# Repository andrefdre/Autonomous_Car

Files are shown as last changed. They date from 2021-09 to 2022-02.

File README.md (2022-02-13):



<!-- PROJECT SHIELDS -->
<!--
*** I'm using markdown "reference style" links for readability.
*** Reference links are enclosed in brackets [ ] instead of parentheses ( ).
*** See the bottom of this document for the declaration of the reference variables
*** for contributors-url, forks-url, etc. This is an optional, concise syntax you may use.
*** https://www.markdownguide.org/basic-syntax/#reference-style-links
-->
[][contributors-url]
[][forks-url]
[][stars-url]
[][issues-url]
[][license-url]
[][linkedin-url]

<!-- PROJECT LOGO -->
<br />
<div align="center">
  <a href="https://github.com/andrefdre/Autonomous_Car">
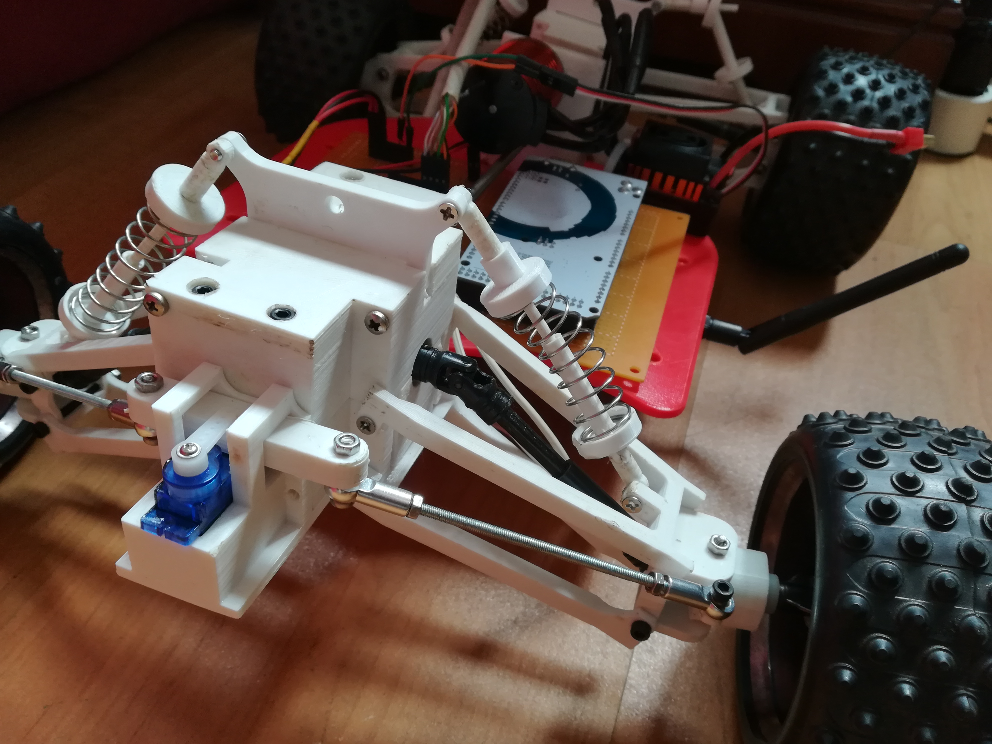
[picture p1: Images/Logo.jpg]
    
  </a>

  <h3 align="center">Autonomous Car</h3>

  <p align="center">
    It's an atounomous car that uses GPS.
    <br />
    <br />
    <a href="https://github.com/andrefdre/Carro/issues">Issues</a>
    ·
    <a href="https://github.com/andrefdre/Carro/projects/1">Project</a>
    ·
    <a href="https://github.com/andrefdre/Carro/wiki">Wiki</a>
  </p>
</div>

<!-- TABLE OF CONTENTS -->
<details>
  <summary>Table of Contents</summary>
  <ol>
    <li><a href="#Introduction">Introducion</a></li>
    <li><a href="#Libraries">Libraries</a> </li> 
    <li><a href="#License">License</a></li>
    <li><a href="#Contact">Contact</a></li>
  </ol>
</details>

<!-- Introduction -->
## Introduction

<p>This projected started in the beggining of my university and I setup myself to build an autonumous car that could drive alone. </p>
<p>The main objective was to make the car and add GPS navigation so it could have coordinates previously set up and then run that course. </p>
<p>So it all started with the mechanical part of the project with the palns to be 4 wheel drive and have a better suspension than the previous version. The components were mostly 3D printed and only the shafts and some other parts where bought. </p>
<p>After that, started the developemnt of the eletrical componnets alongside the programming of the code. This part was the most difficult since I had lots of problems with the communication beetwen the car and the controller.  </p>
<p>The previous version used bluetoth chips but since the range was very limited i eventualy changed to RF24 chips wich use radio waves that has more range.  </p>

<p> Previous version: </p> 
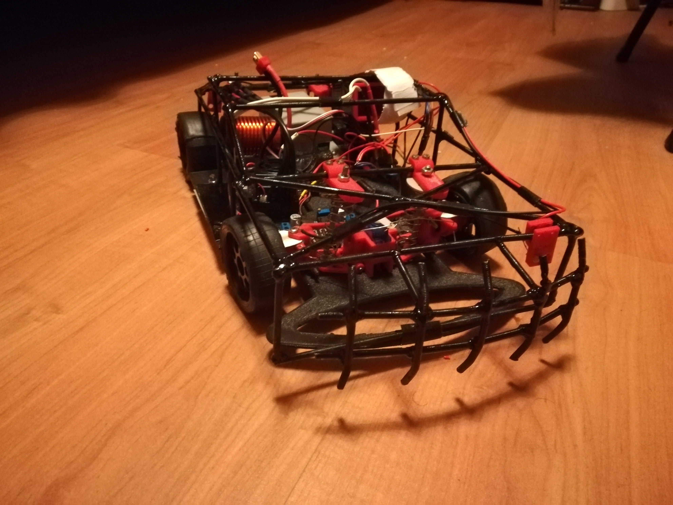
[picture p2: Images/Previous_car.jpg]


For more see the [open issues](https://github.com/andrefdre/Carro/issues) for a full list of proposed features (and known issues).

<p align="right">(<a href="#top">back to top</a>)</p>

<!-- Required_Libraries -->
## Libraries 

The arduino code requires some dependencies:
<ol>
    <li><a href="https://github.com/embeddedartistry/arduino-printf">LibPrintf</a></li>
    <li><a href="https://forum.hobbycomponents.com/viewtopic.php?t=2034">HCPCA9685</a> </li> 
    <li><a href="https://www.arduino.cc/en/reference/SPI">SPI</a></li>
    <li><a href="https://github.com/nRF24/RF24">RF24</a></li>
    <li><a href="https://www.arduino.cc/reference/en/libraries/libprintf/">LibPrintf</a></li>
  </ol>

<p align="right">(<a href="#top">back to top</a>)</p>

<!-- LICENSE -->
## License

Distributed under the GNU GENERAL PUBLIC LICENSE. See `LICENSE.txt` for more information.

<p align="right">(<a href="#top">back to top</a>)</p>

<!-- CONTACT -->
## Contact

André Cardoso - andref@ua.pt

Project Link: [https://github.com/andrefdre/Carro](https://github.com/andrefdre/Carro)

<p align="right">(<a href="#top">back to top</a>)</p>

<!-- MARKDOWN LINKS & IMAGES -->
<!-- https://www.markdownguide.org/basic-syntax/#reference-style-links -->
[contributors-shield]: https://img.shields.io/github/contributors/andrefdre/Carro.svg?style=for-the-badge
[contributors-url]: https://github.com/andrefdre/Carro/graphs/contributors
[forks-shield]: https://img.shields.io/github/forks/andrefdre/Carro.svg?style=for-the-badge
[forks-url]: https://github.com/andrefdre/Carro/network/members
[stars-shield]: https://img.shields.io/github/stars/andrefdre/Carro.svg?style=for-the-badge
[stars-url]: https://github.com/andrefdre/Carro/stargazers
[issues-shield]: https://img.shields.io/github/issues/andrefdre/Carro.svg?style=for-the-badge
[issues-url]: https://github.com/andrefdre/Carro/issues
[license-shield]: https://img.shields.io/github/license/andrefdre/Carro.svg?style=for-the-badge
[license-url]: https://github.com/andrefdre/Carro/blob/main/LICENSE
[linkedin-shield]: https://img.shields.io/badge/-LinkedIn-black.svg?style=for-the-badge&logo=linkedin&colorB=555
[linkedin-url]: https://www.linkedin.com/in/andr%C3%A9-cardoso-8bb264223/
[product-screenshot]: Images/Logo.jpg

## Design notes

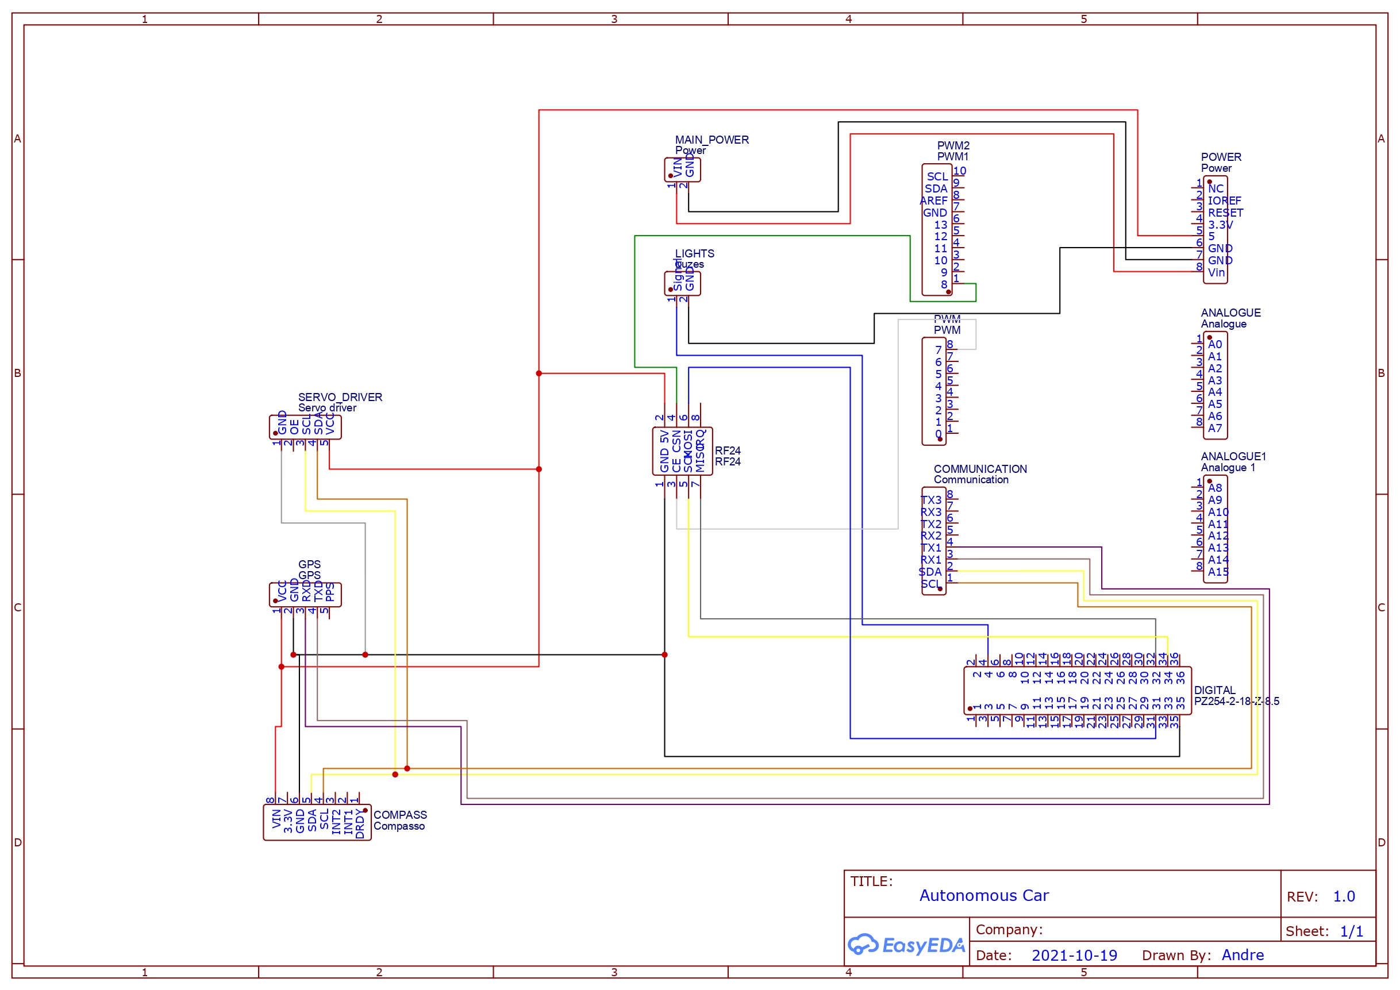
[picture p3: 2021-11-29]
Images/Schematic_Car.jpg

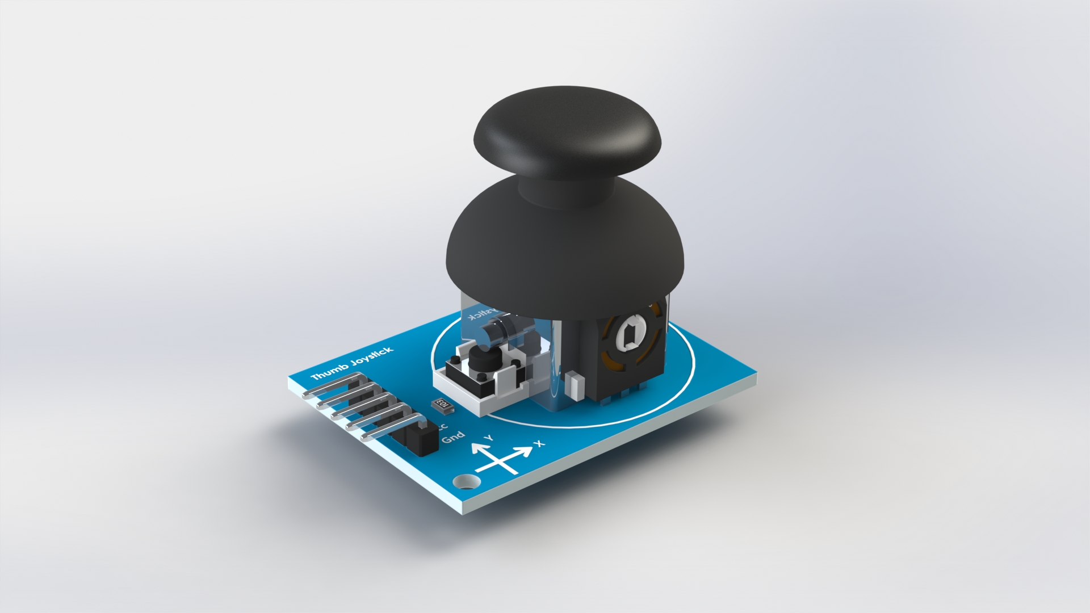
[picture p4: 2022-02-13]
Mechanical_project.psd/Controller/Imported/Joystick/PS2 Joystick Module 3D View.JPG

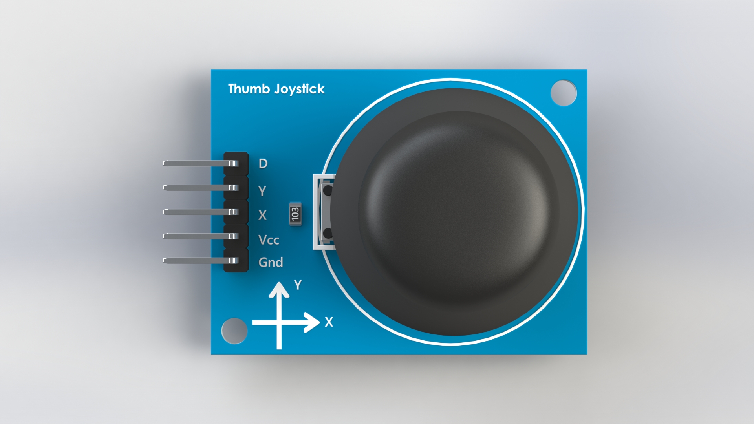
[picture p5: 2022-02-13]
Mechanical_project.psd/Controller/Imported/Joystick/PS2 Joystick Module Top View.JPG

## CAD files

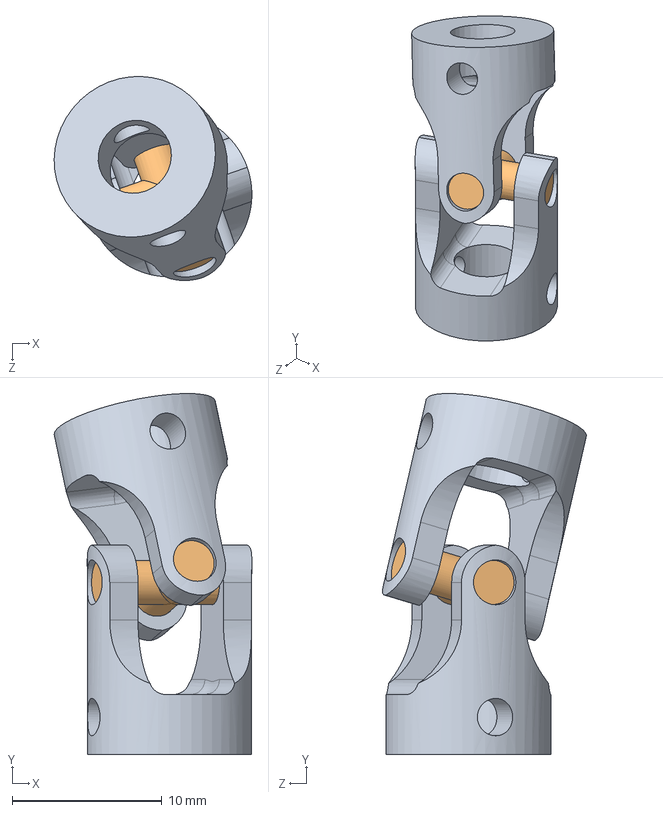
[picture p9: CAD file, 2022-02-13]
Mechanical_project.psd/Car/assemblie/U-joint.SLDASM
13.2 x 24.1 x 13.6 mm
u-joint x 2
u-joint middle

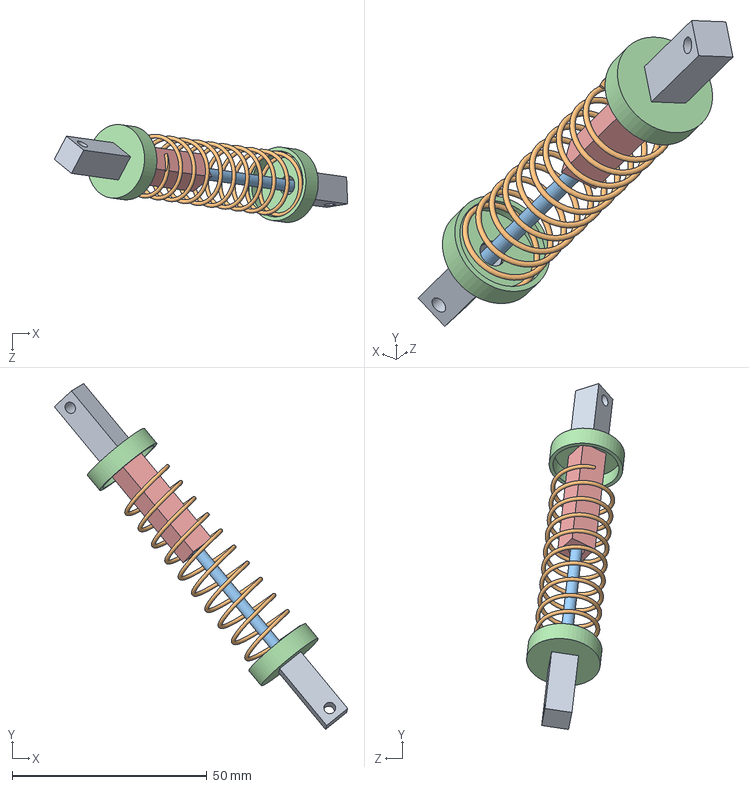
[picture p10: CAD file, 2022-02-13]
Mechanical_project.psd/Car/suspension/suspension rear left.SLDASM
75.3 x 88.8 x 25.2 mm
ball joint x 2
Spring
suspension shaft
washer x 2
suspension shaft 1

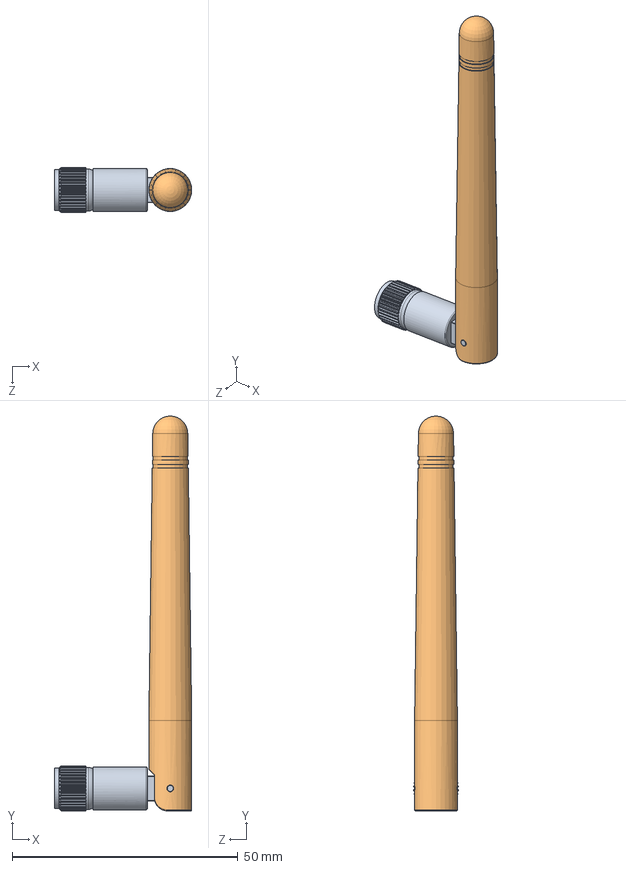
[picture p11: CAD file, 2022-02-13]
Mechanical_project.psd/downloaded/nrf24/NRF24L01L + Antenna 2.4 GHz/Antenna assy.SLDASM
30.5 x 87.5 x 9.98 mm
Antenna base
Antenna top

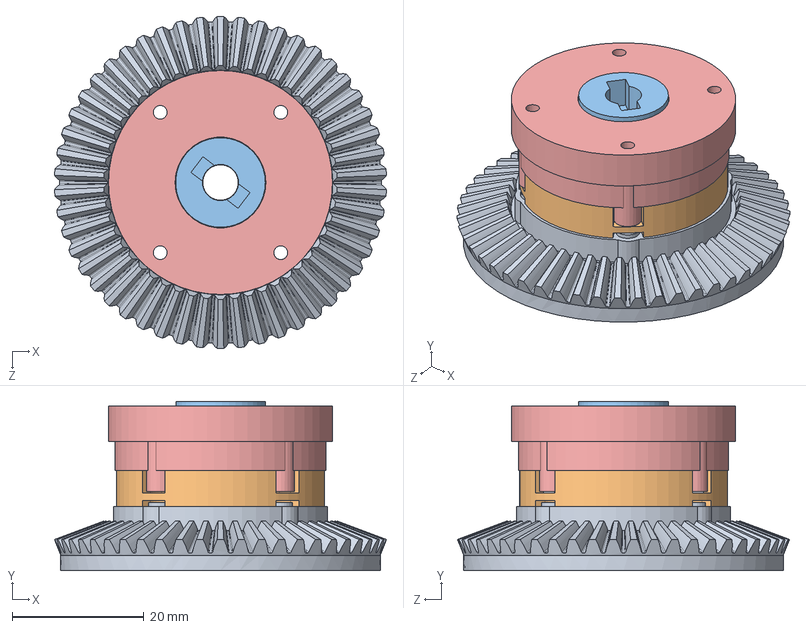
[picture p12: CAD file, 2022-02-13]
Mechanical_project.psd/Car/assemblie/Diferencial rodas.SLDASM
50.4 x 25.7 x 50.4 mm
anel versao 3
planeta x 2
sol x 2

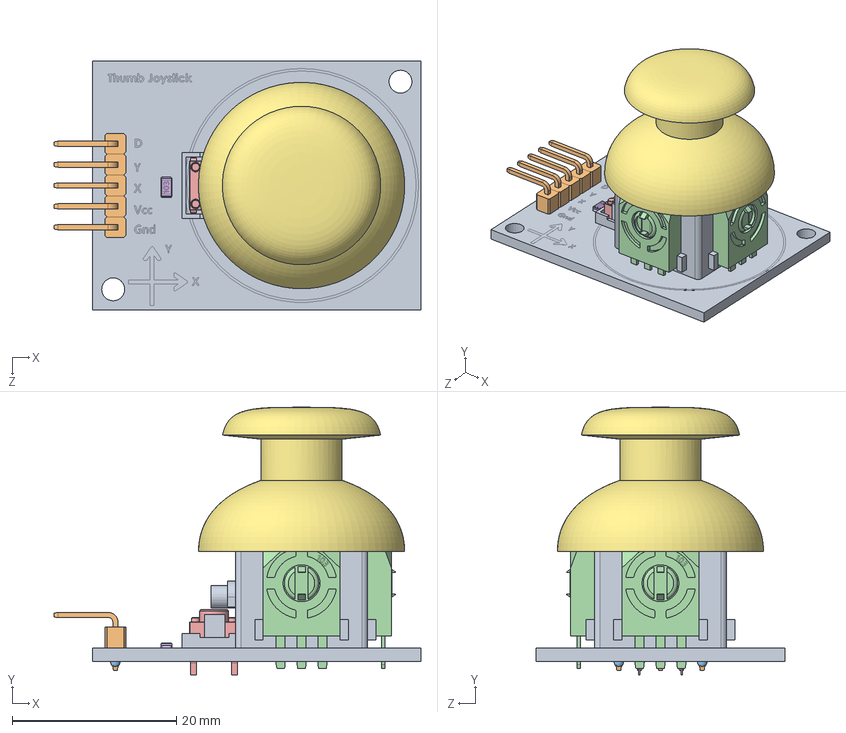
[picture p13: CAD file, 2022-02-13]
Mechanical_project.psd/Controller/Imported/Joystick/PS2 Joystick Module.SLDASM
44.7 x 32.6 x 30.3 mm
ps2board
90headerMale x 5
solder x 5
verticalTrimmer103 x 2
pushButton1_5mm
smdResistor103
Thumbstick

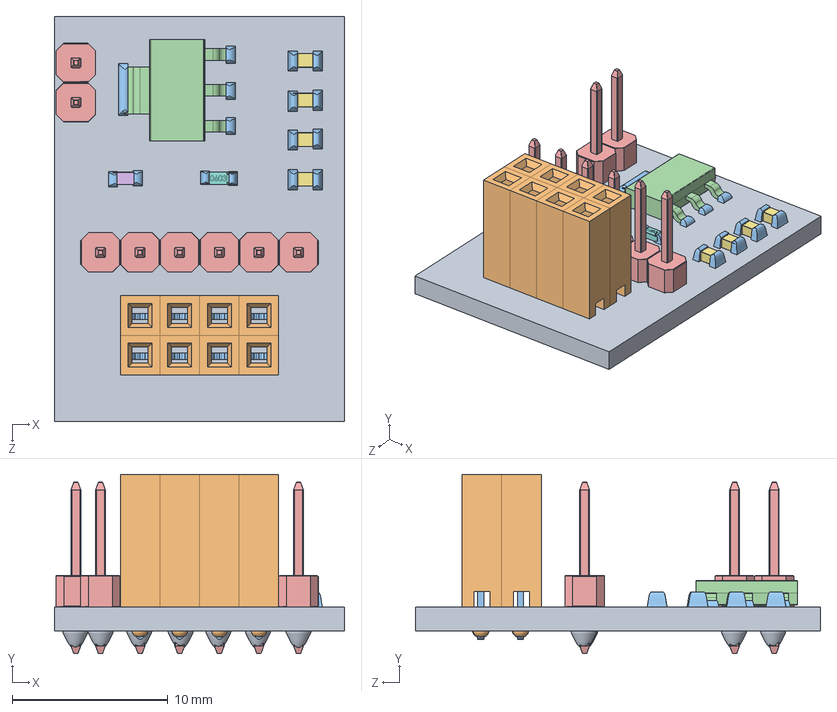
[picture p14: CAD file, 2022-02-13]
Mechanical_project.psd/downloaded/nrf24/NRFL24L01_Power_Board_asm.SLDASM
18.6 x 11.5 x 26.0 mm
nRF24L01_power_board_PCB
header x 8
pin x 8
SOT-223
Strait_Headers x 2
User Library-LED 0603
User Library-CAPC1608X09 x 4
User Library-RES_1609-0603
Solder x 9
Solder2 x 8
Solder3 x 16

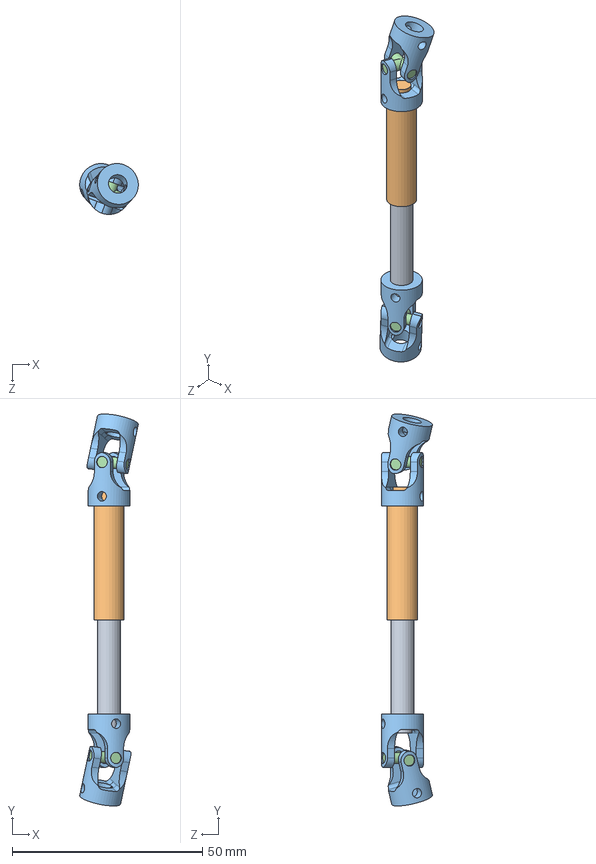
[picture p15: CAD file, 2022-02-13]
Mechanical_project.psd/Car/assemblie/Ujoin axle.SLDASM
15.4 x 102.9 x 13.4 mm
eixo ujoint inner
eixo ujoint outside
u-joint x 4
u-joint middle x 2

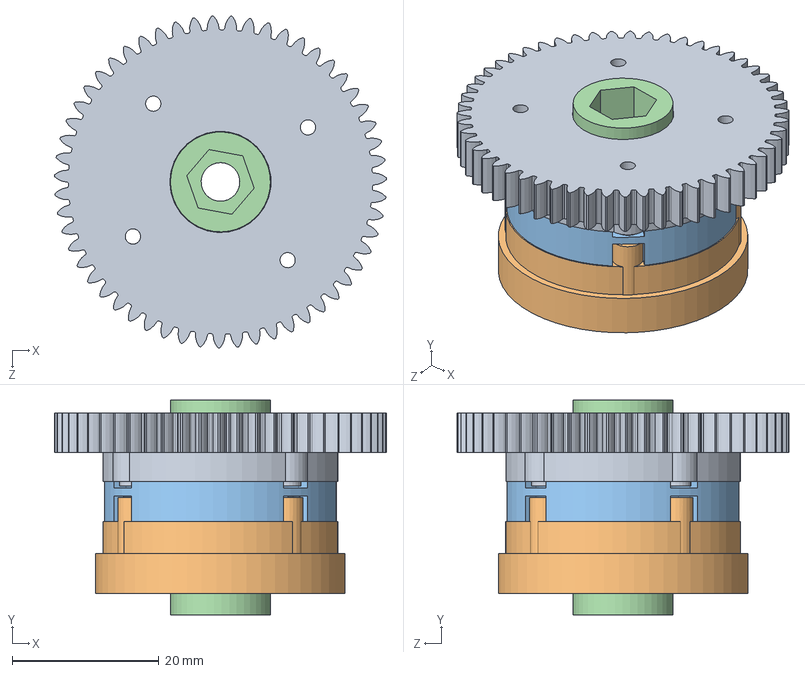
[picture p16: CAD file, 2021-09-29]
Mechanical_project.psd/Car/assemblie/planetery.SLDASM
45.2 x 29.3 x 45.2 mm
anel
anel 2
middle part of the planetery
planeta x 2
sol x 2

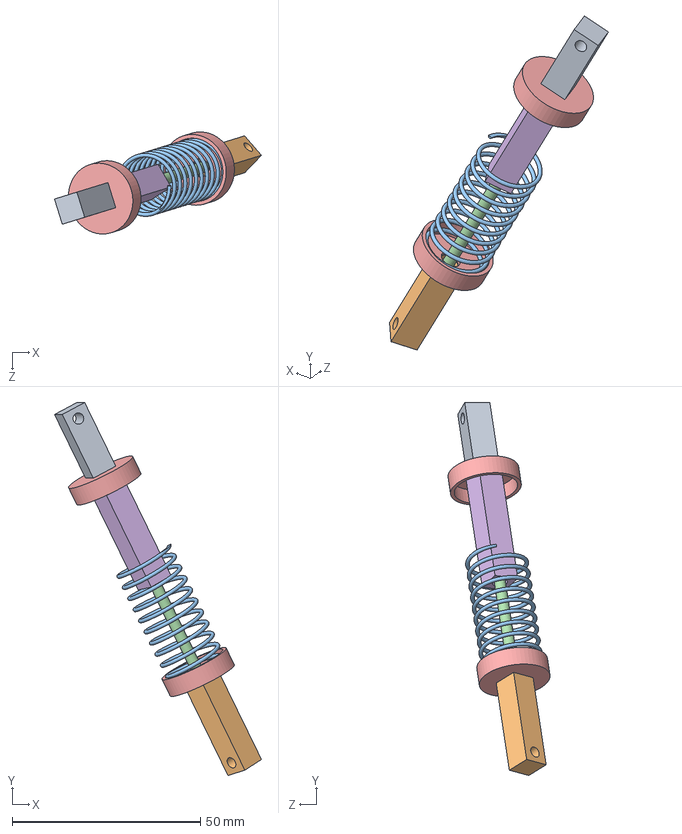
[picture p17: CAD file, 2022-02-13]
Mechanical_project.psd/Car/suspension/suspension front right.SLDASM
55.0 x 99.1 x 27.1 mm
ball joint
ball joint down
Spring front
suspension shaft
washer x 2
suspension shaft 1

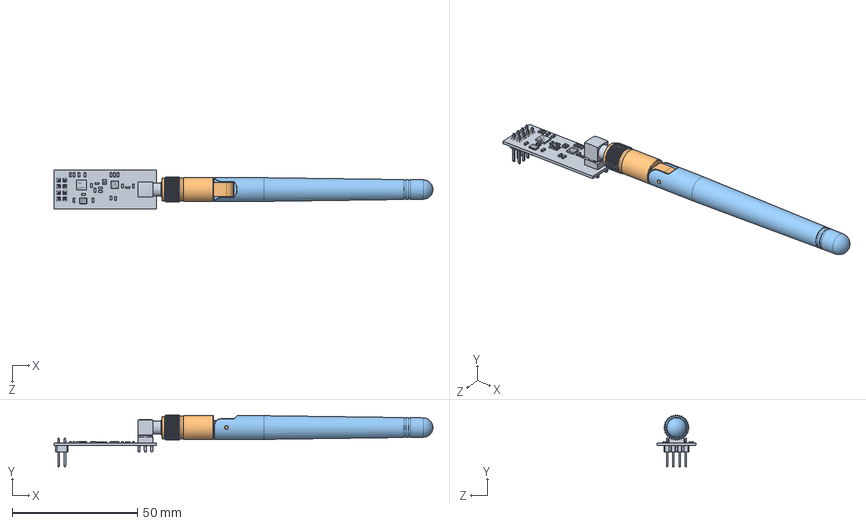
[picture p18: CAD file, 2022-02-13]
Mechanical_project.psd/downloaded/nrf24/NRF24L01L + Antenna 2.4 GHz/NRF24L01L+Antenna.SLDASM
151.4 x 20.7 x 15.5 mm
NRF24L01L
Antenna base
Antenna top

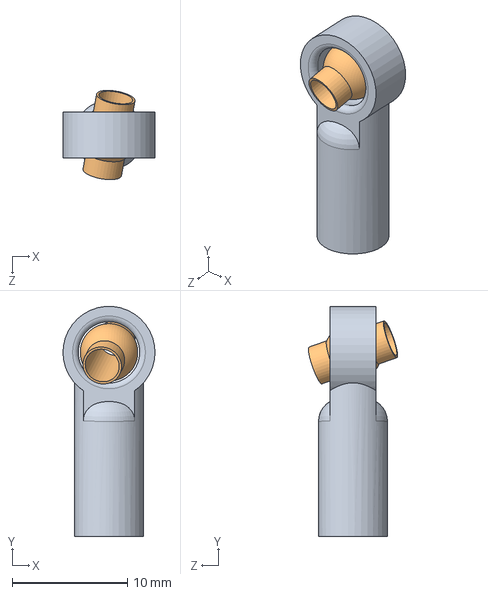
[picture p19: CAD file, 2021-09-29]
Mechanical_project.psd/Car/assemblie/Ball Joint.SLDASM
8.00 x 20.0 x 7.76 mm
Ball Joint Steer
Ball Joint Steer 1

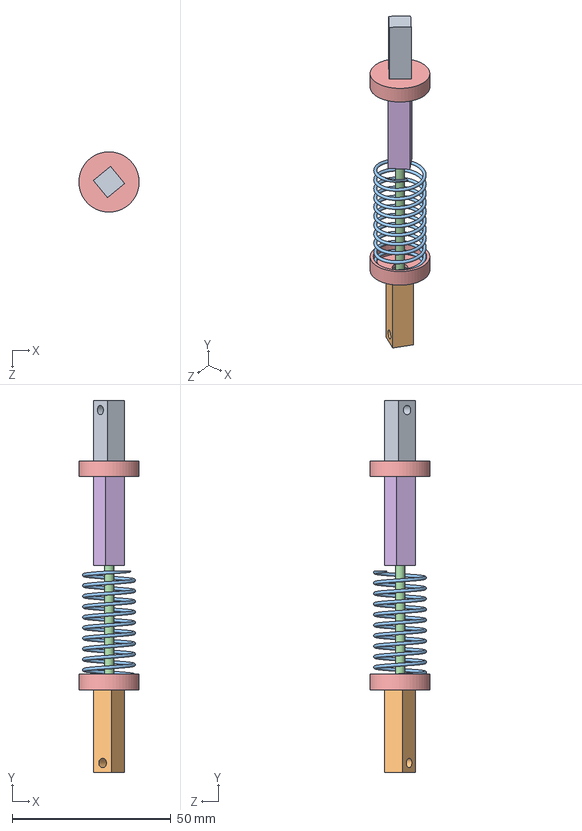
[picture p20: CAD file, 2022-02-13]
Mechanical_project.psd/Car/suspension/suspension front left.SLDASM
19.0 x 117.2 x 19.0 mm
ball joint
ball joint down
Spring front
suspension shaft
washer x 2
suspension shaft 1

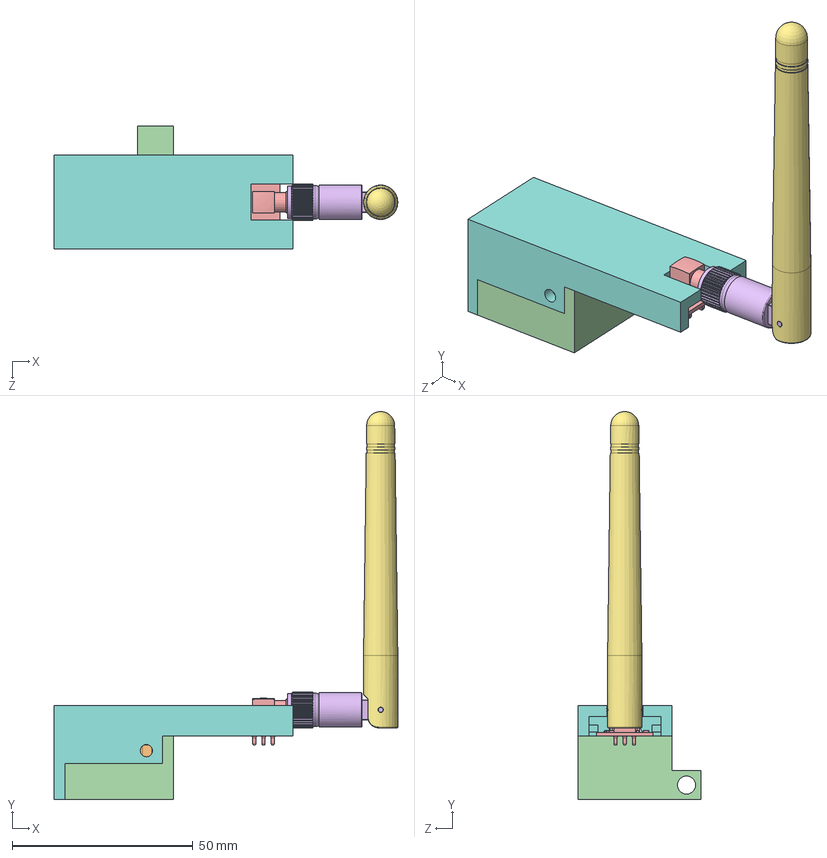
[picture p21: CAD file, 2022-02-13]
Mechanical_project.psd/downloaded/nrf24/NRF24L01_asm.SLDASM
95.1 x 107.3 x 34.0 mm
nRF24L01_power_board_PCB
header x 8
pin x 8
SOT-223
Strait_Headers x 2
User Library-LED 0603
User Library-CAPC1608X09 x 4
User Library-RES_1609-0603
Solder x 9
Solder2 x 8
Solder3 x 16
NRF24 box bottom
NRF24L01L
Antenna base
Antenna top
NRF24 box top

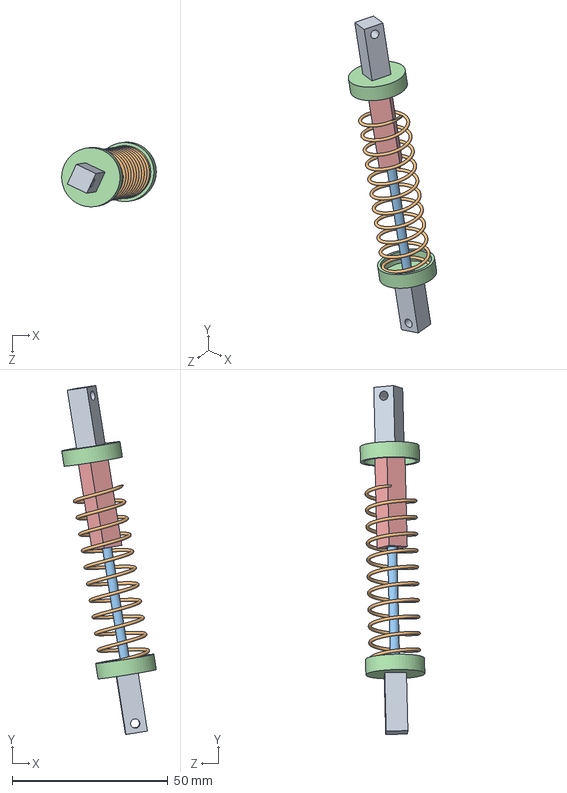
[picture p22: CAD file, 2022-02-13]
Mechanical_project.psd/Car/suspension/suspension rear right.SLDASM
30.4 x 112.2 x 20.8 mm
ball joint x 2
Spring
suspension shaft
washer x 2
suspension shaft 1

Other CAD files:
Mechanical_project.psd/downloaded/SG90 - Micro Servo 9g - Tower Pro.SLDASM
Mechanical_project.psd/downloaded/nrf24/Header_4.SLDASM
Mechanical_project.psd/downloaded/nrf24/header.SLDASM
Mechanical_project.psd/Car/suspension/suspension.SLDASM
Mechanical_project.psd/Car/2 gear.SLDPRT
Mechanical_project.psd/Car/BDESC-S10E-RTR brushed motor speed controller ESC.stp.SLDPRT
Mechanical_project.psd/Car/Ball Joint Steer 1.SLDPRT
Mechanical_project.psd/Car/Ball Joint Steer.SLDPRT
Mechanical_project.psd/Car/Battery 1500 cover.SLDPRT
Mechanical_project.psd/Car/Battery 1500.SLDPRT
Mechanical_project.psd/Car/Battery 4500 cover.SLDPRT
Mechanical_project.psd/Car/Battery 4500.SLDPRT
Mechanical_project.psd/Car/Braco inferior-frente.SLDPRT
Mechanical_project.psd/Car/Braco inferior.SLDPRT
Mechanical_project.psd/Car/Braco superior frente.SLDPRT
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

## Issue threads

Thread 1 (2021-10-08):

Remaking PCB due to bad ground

andrefdre, 2021-10-08:
When comunicating beetwen the car and the controller the information has interference.
This interference seems to be done by a bad ground on the board pcb.

andrefdre, 2021-11-28:
The PCB has arrived but due to the pins being lost in the delivery the remaking was delayed

andrefdre, 2021-12-07:
The PCB was mostly redone but due to bad wiring in the cable that goes to the RF24 module it need to change the pins layout

andrefdre, 2021-12-30:
After some tests confirmed the pcb from the arduino to the RF24 board is okay so the cable is at fault and needs to be shortned and replaced. While doing the tests ended up destroying the controller pcb since was made from the yellow ones which will now replace with the green ones since they last much longer. Also will create a 3D model for the controller so will create a new issue with the aspect of remaking the controller

andrefdre, 2022-02-09:
The pcb was remade and the main functions were implemented. The other functions like GPS and Compass will be added as needed. Since the PCB was remade the issue will be closed.

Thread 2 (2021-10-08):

Stop using Serial.print to increase sketch speed

andrefdre, 2021-10-08:
One problem noted on the code was that when printing to serial the code got alot slower increasing interferences in the communication.

andrefdre, 2021-11-18:
Already updated the code to implement this function. Only need to wait for the pcb to be redone so it can be tested and see if there were improvements in the speed.

andrefdre, 2021-12-16:
The code doesn't seem to work with all the parameters inside the same line. Have to see how to concatenate the strings.

Closed 2022-02-18.

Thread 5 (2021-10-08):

Add a compass to the car

andrefdre, 2021-10-08:
Add a compass to the car so it knows what direction its going without depending on the Gps chip

andrefdre, 2021-11-28:
This was added to the car but had to be removed temporarily since there was having communication problems so was reverted to check if it was causing the problem wich wasn't the case

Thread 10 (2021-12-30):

Remaking the controller

andrefdre, 2021-12-30:
This issue was created after working on the PCB for the car and ended up realizing there need to be made an improvement to the controller PCB too and create 3D models for the controller so the parts can be 3D printed instead of being handmade with acrylic

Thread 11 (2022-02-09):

Problem controlling the ESC with PCA9685s

andrefdre, 2022-02-09:
The esc doesn't configurate by itself while powering up. While trying to configure manually wasn't able to make it properly work.
After some research found that the Adafruit PCA9685 library might be better than the HCPCA9685 wich is the one currently implemented.
More tests will be done during the week

andrefdre, 2022-02-09:
After some research there needs to be found the min and the max of the esc and the servo and then map the values that are in degrees to that respective value

andrefdre, 2022-02-09:
After some testing and changing to Adafruit library it started working. But the results don't quite make sense. For the servo everything was as expected, the min and max pulse corresponded to 150 and 600 wich in microseconds, from what the library says, it corresponds to 600 to 2400. Which is closely to the datasheet that says 500 to 2500.
While for the motor it was expect for the value in microseconds to be between 1000 and 2000, which can't be confirmed yet since I have no access to one, but the pulse length in the code was 170 to 370 which wasn't the one calculated by doing a simple relation with the servo values. This concludes that there needs to be more tweaking done to the servo values and the ESC ones and also investigating the width in microseconds of the waves.
There is also worth mentioning that the frequency must also be checked.
The only problem with all this is that I have no access to an oscilloscope

andrefdre, 2022-02-11:
To solve the problem there is two commands to control the servo driver and changed from pwm to microseconds since the pwm one wasn't making sense the values that were being used for the motor. With the microseconds it can be directly input the information that is available in the datasheet, which for the servo is 500 to 2500 microseconds and for the motor is 1000 to 2000 microseconds (needs a bit more research on this value since I have no datasheet available for it, so just used a generic value for ESC). From previous research this command was slower cause internally it was doing conversion to the previous command, but from tests in the worktable seems fast enough, needs real testing.

andrefdre, 2022-02-11:
The next step is testing everything in the car. Which will probably be done during next week

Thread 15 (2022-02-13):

Problem with back wheels bearing

andrefdre, 2022-02-13:
Has expected the bearing in the back wheels don't have a way to be locked and due to using there builds slack in the fit and they get out. A new way of assembling must be studied and a way that will be approached will be based on the front wheels setup.

andrefdre, 2022-02-15:
New Hubs were made. There needs to be printed and tested.
During the tests made during the day it happened what was expected, this is, the wheels kept coming out

andrefdre, 2022-02-17:
New parts were printed, they are assembled as front wheels. For now seems it's working fine but real testing needs to be done.
If no more problems surge this issue will stay closed.

Closed 2022-02-17.

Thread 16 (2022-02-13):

Automatic establish connection

andrefdre, 2022-02-13:
A new feature that will be worked on is the feature to reestablish the connection after it has been lost and the speed and steer parameters have been reset.
One way of implementing is establish a timer that turns on after losing connection and and after a while reset the connection.

andrefdre, 2022-02-15:
After some research this seems to be impossible if the problem caused by the disconnections is made by bad connection. More research is needed but one solution to solve this issue is use a transistor reinitialize the nrf24 module. Other solution is make separate cables for ground and Vin to the nrf24 cause as currently the big cable is pulling the connectors of this 2 wires out and is what I think is causing the connection problems. During the week will be made new cable for power.

andrefdre, 2022-02-17:
There was made a separate cable for the power and ground wires separate to the communication ones so it doesn't keep pulling it out. Seems to have fixed the problems and the connection seems a lot more sturdy.
There was made an implementation to the code to reestablish the connection, this only work if the connection was lost due to the controller getting disconnected or the distance increase past the limit and when there are new connection available it reconnects.
Needs more testing in real world situations but seems fixed for now, so the issue will be closed until further problems surge.

Closed 2022-02-17.

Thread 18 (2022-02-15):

Changes in mechanical components after tests

andrefdre, 2022-02-15:
During the day there was made tests and was noticed that the back wheel keeps coming off along side the bearing and shaft this is due to the bearing being only press fitted. This is going to be resolved changed the way its assembled and make it like front wheels.
There was noticed a big clearance gap in the front wheel hubs making the wheel tilt inside, new models are currently being printed to test hoping to fix this problem.

andrefdre, 2022-02-17:
There were mounted new parts to solve all the problems listed above. At first glance it seems to have solved all the problems, but real testing is needed. This issue will be closed and if changes are needed it will be reopened.

Closed 2022-02-17.

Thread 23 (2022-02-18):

Add mechanical breaks using a servo

andrefdre, 2022-02-18:
Since I can't configure the ESC I can't enable the brake function. Since the car needs to stop there needs to be implemented brakes in the car. One way of doing this is using a system like real cars but instead of applying it to all wheels only apply it to the  main axis

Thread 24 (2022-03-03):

Gear ratio

andrefdre, 2022-03-03:
Since the car is made from brittle materials there is no point in having a large top speed, instead it's beneficial to have a small top speed and a bigger acceleration improving the starting motion since it's not a closed loop motor

andrefdre, 2022-03-03:
Currently this is the gear teeth:
Gear motor: 16
Main shaft: 39
Gearbox in: 21
Gearbox out: 48

Wheel diameter: 100mm
Motor rpm: 50000rpm

andrefdre, 2022-07-22:
After some months away of the project finally back and started doing some changes. Made a new gearbox, the only problem now is solving where to put the PCB which need to have it in person in order to take some measurements and then compare with the 3D model One way to solve this is place the PCB on top of the car, needs some brainstorming.

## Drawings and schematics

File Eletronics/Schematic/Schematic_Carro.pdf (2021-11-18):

A

A

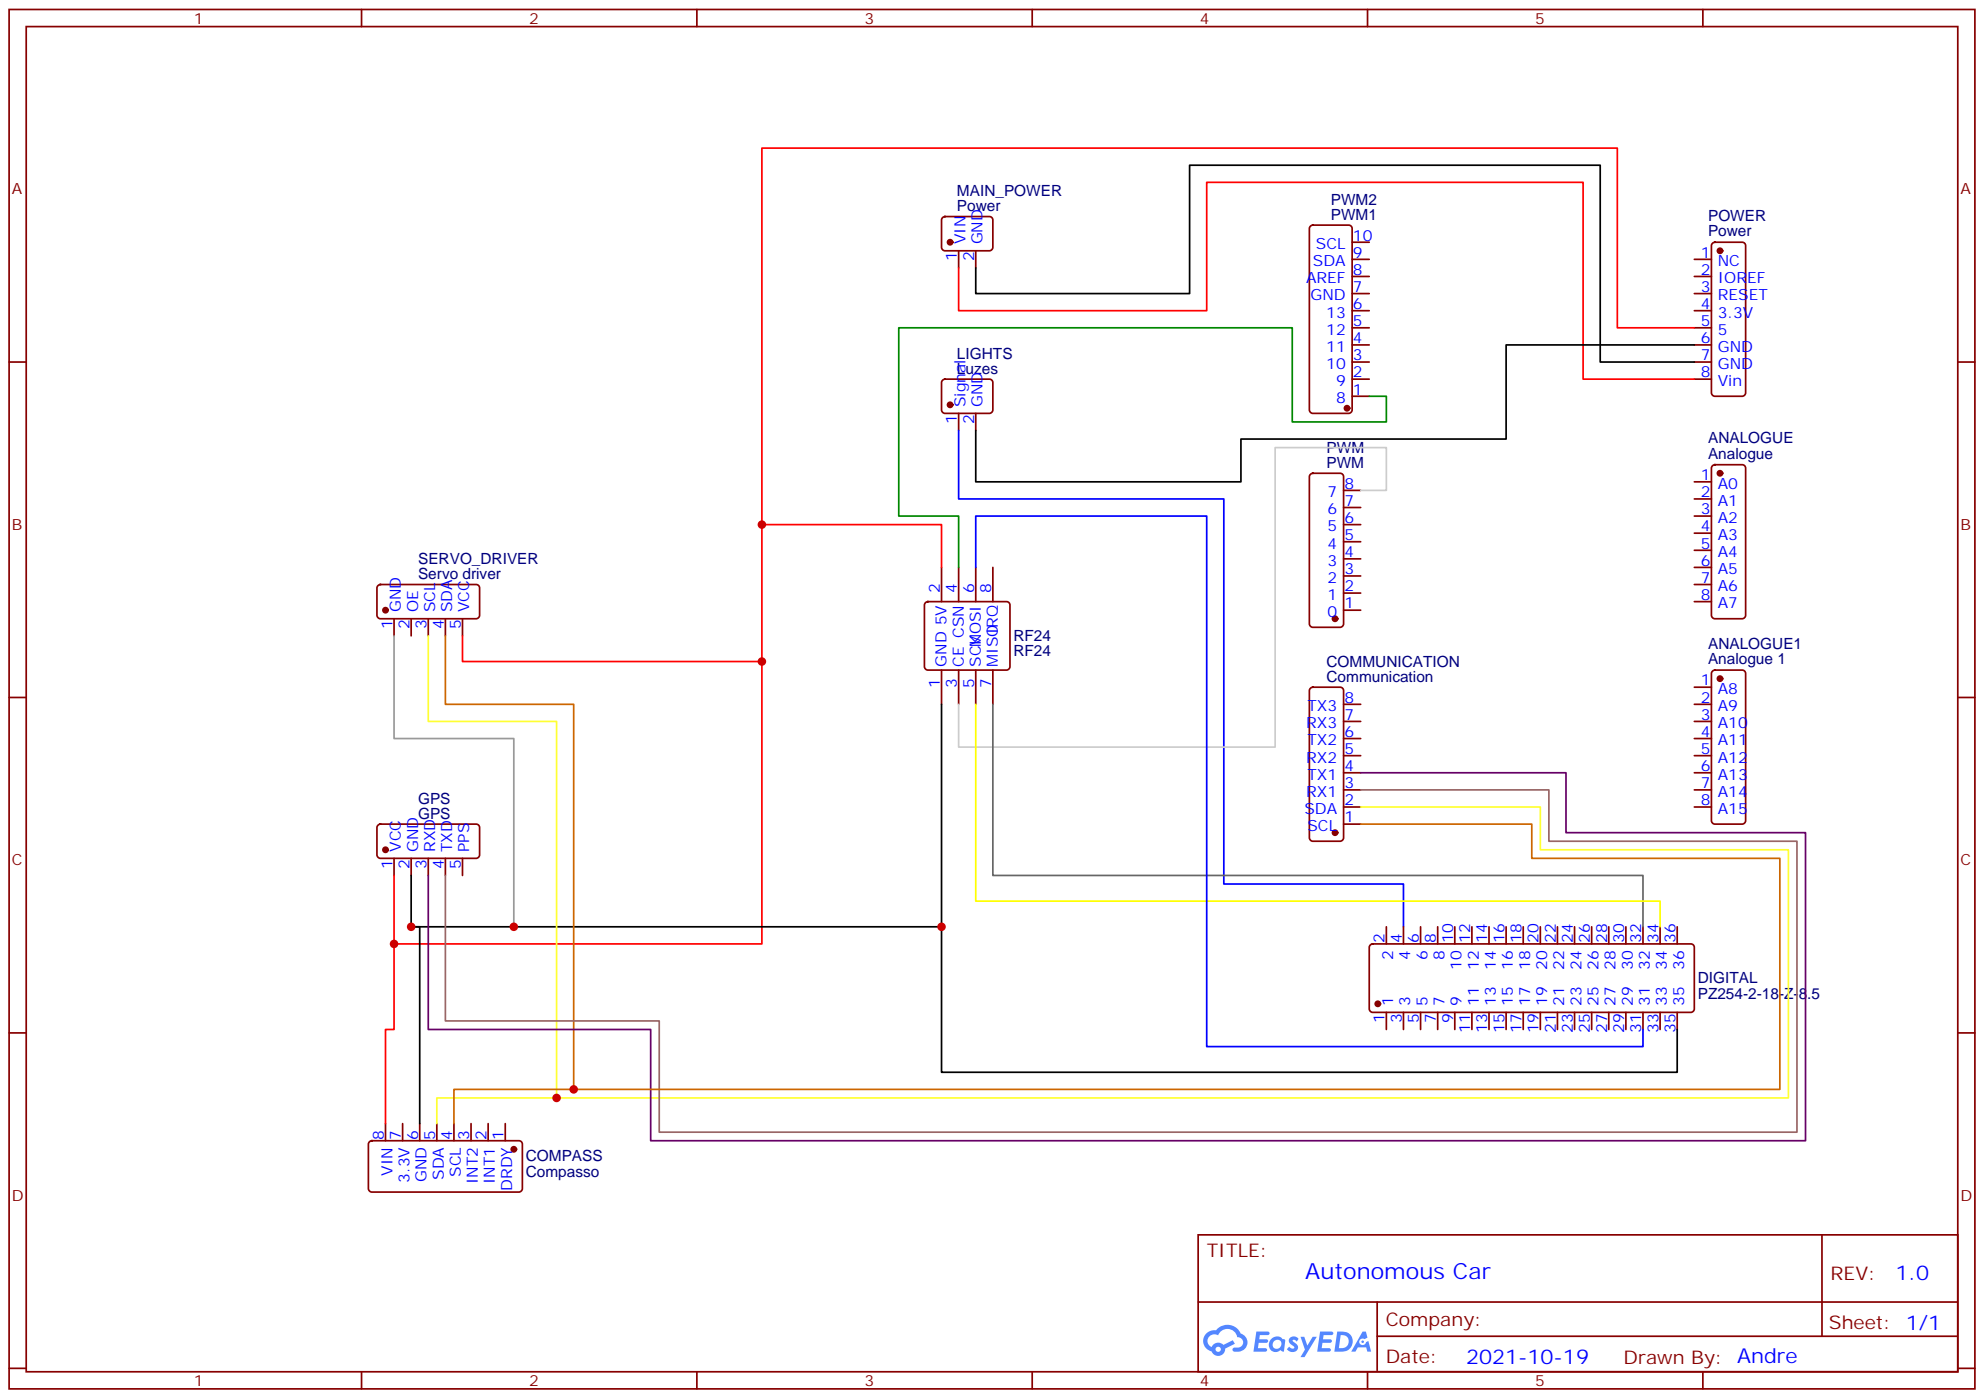
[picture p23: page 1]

DRDY 1 INT1 2 INT2 3 SCL 4 SDA 5 GND 6 3.3V 7 VIN 8

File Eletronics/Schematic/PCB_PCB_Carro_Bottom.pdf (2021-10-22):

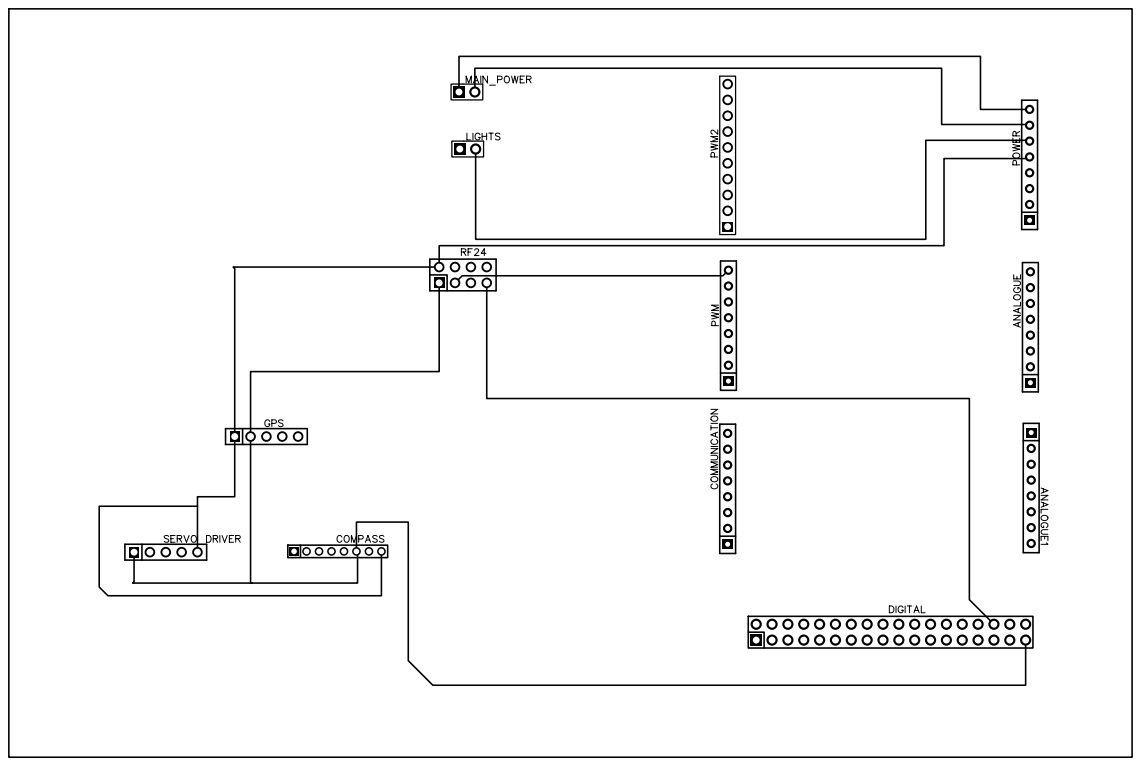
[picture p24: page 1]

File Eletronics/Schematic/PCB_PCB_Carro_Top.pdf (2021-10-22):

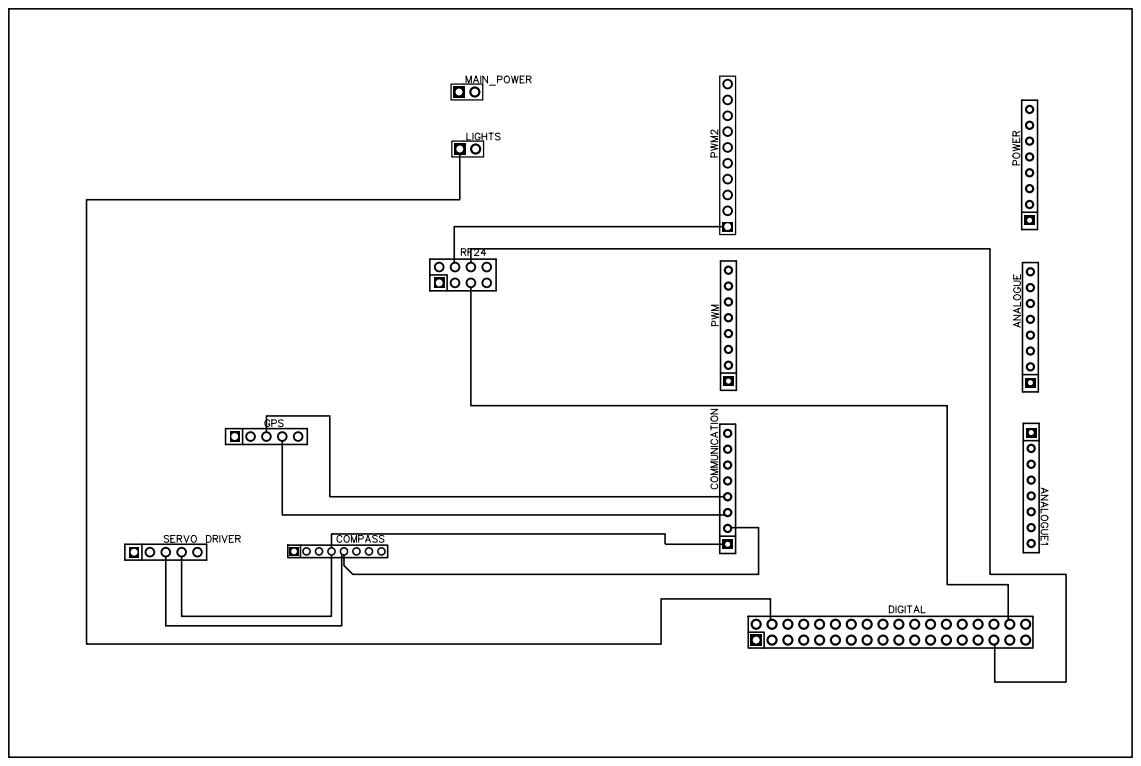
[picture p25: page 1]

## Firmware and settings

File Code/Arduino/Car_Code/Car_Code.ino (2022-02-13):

/*
  Autonomous Car

  The code first checks if it is still receiving information, if it is then keep receiving and then send use that information to control the servo and the motor. In the end
  send the information to the serial for debbguing purposes.

  Components:
  - Arduino Mega 2560
  - RF24 module
  - pca9685s
  - DS3235SG
  - 9T 4370KV Metal Brushless Motor
  - 60A ESC
  - Lipo battery 11,1V 3S 45C 4500mAh
  - Lipo battery 11,1V 3S 40C 1500mAh

  PinOut:
  *RF24
   -

  https://github.com/andrefdre/Carro
*/

// Library
#include <LibPrintf.h> //Includes the Libprintf library to use the printf function to write to serial
#include <Wire.h>
#include <Adafruit_PWMServoDriver.h>
#include <SPI.h>      //Required library for RF24 communication
#include <nRF24L01.h> //Includes the library for the communication with radio waves
#include <RF24.h>     //Includes the library for the communication with radio waves

Adafruit_PWMServoDriver pwm = Adafruit_PWMServoDriver();

// RF24
const byte slaveAddress[6] = "00001"; // Sets the address for communitating with the controller(must be the same in the controller)
RF24 radio(7, 8);                     // CE Pin, CSN Pin

// Structure with the received information
struct RECEIVE_DATA_STRUCTURE
{
  int velocity;
  int steer;
  int light;
  int slow;
  int alone;
  int vmais;
};
RECEIVE_DATA_STRUCTURE mydata; // Atributes a easier name to be used in the structure

// General variables
#define Baud 115200   // Sets the communication baudRate with the computer
#define center 90     // Center of the wheels
#define steervalue 22 // Defines the amount the wheels will turn
#define lightpin 22   // Defines the light pin
#define motorPin 0    // Define the motor pin
#define servoPin 1    // Define the servo pin
#define SERVOMIN 500  // Defines the min pulse for servo
#define SERVOMAX 2500 // Defines the max pulse for servo
#define MOTORMiN 1000 // Defines the min pulse for motor
#define MOTORMAX 2000 // Defines the max pulse for motor

// Variables
bool rslt;              // Stores the result of the communication
int light1 = 0;         // Lights value(0-off, 1-on)
long previoustime = 0;  // Time the lights value was changed
long time3 = 0;         // Time for the commutation of the light pin
long previoustime1 = 0; // Last time it was received communication
long time1 = 0;         // Time to check if the arduino is still communicating with controller
long previoustime2 = 0; // Time the modo was changed
long time2 = 0;         // Time for the commutation of the modo
int mode = 0;           // Defines if its in automatic mode or manual mode (0-manual, 1-automatic)
int motor_pulselength;  // Declares the variable that be used to map the value from degrees to microseconds pwm wave for motor
int servo_pulselength;  // Declares the variable that be used to map the value from degrees to microseconds pwm wave for servo

void setup()
{
  // Serial communication
  Serial.begin(Baud); // Initializes Serial communication with the computer for debugging

  // HCPCA9685
  pwm.begin();                                                 // Initializes the PWM driver
  pwm.setOscillatorFrequency(27000000);                        // Value that needs to be adjusted to have a perfect 50hz (need an oscilloscope to check this)
  pwm.setPWMFreq(50);                                          // Sets the frequency of the servos which tipically is 50
  motor_pulselength = map(90, 0, 180, MOTORMiN, MOTORMAX);     // Maps the the angle value to PWM microseconds
  pwm.writeMicroseconds(motorPin, motor_pulselength);          // Writes to the motor to neutral position
  servo_pulselength = map(center, 0, 270, SERVOMIN, SERVOMAX); // Maps the the angle value to PWM microseconds
  pwm.writeMicroseconds(servoPin, servo_pulselength);          // Writes for the servo to center the wheels

  // Lights
  pinMode(lightpin, OUTPUT);   // Initializes light Pin
  digitalWrite(lightpin, LOW); // Starts the lights as turnoff

  // SPI
  SPI.setClockDivider(100000);
  SPI.setDataMode(SPI_MODE0); // try mode 0 1 2 3

  // RF24
  if (!radio.begin())
  {
    Serial.println(F("radio hardware is not responding!!"));
    while (1)
    {
    } // hold in infinite loop
  }
  radio.openReadingPipe(0, slaveAddress); // Opens a pipe to communicate(must be the same as the controller) with the controller
  radio.startListening();                 // Sets the RF24 driver to listening for new information

  // Arduino setup Check
  printf("Arduino Initialized"); // Checks if the arduino setups correctly
}

void loop()
{
  // Checks if the arduino is still receiving information through radio waves, if not centers the wheels and puts it in neutral
  if ((time1 - previoustime1) >= 20)
  {
    motor_pulselength = map(90, 0, 180, MOTORMiN, MOTORMAX);     // Maps the the angle value to PWM microseconds
    pwm.writeMicroseconds(motorPin, motor_pulselength);          // Writes to the motor to neutral position
    servo_pulselength = map(center, 0, 270, SERVOMIN, SERVOMAX); // Maps the the angle value to PWM microseconds
    pwm.writeMicroseconds(servoPin, servo_pulselength);          // Writes for the servo to center the wheels
    mydata.steer = center;
    mydata.velocity = 90;
  }

  else
  {
    // Nrf24
    if (radio.available())
    {                                      // Looking for the data.
      radio.read(&mydata, sizeof(mydata)); // Reading the data
      previoustime1 = time1;               // Reset the time variable
    }
  }
  // Checks the received information is within accepted values and then sends it to the servo driver
  if (mydata.steer < center - steervalue || mydata.steer > center + steervalue || mydata.velocity > 90 + mydata.vmais || mydata.velocity < 90 - mydata.vmais)
  {
    motor_pulselength = map(90, 0, 180, MOTORMiN, MOTORMAX);     // Maps the the angle value to PWM microseconds
    pwm.writeMicroseconds(motorPin, motor_pulselength);          // Writes to the motor to neutral position
    servo_pulselength = map(center, 0, 270, SERVOMIN, SERVOMAX); // Maps the the angle value to PWM microseconds
    pwm.writeMicroseconds(servoPin, servo_pulselength);          // Writes for the servo to center the wheels
  }
  else
  {
    motor_pulselength = map(mydata.velocity, 0, 180, MOTORMiN, MOTORMAX); // Maps the the angle value to PWM microseconds
    pwm.writeMicroseconds(motorPin, motor_pulselength);                   // Writes the mapped value to change the motor speed
    servo_pulselength = map(mydata.steer, 0, 270, SERVOMIN, SERVOMAX);    // Maps the the angle value to PWM microseconds
    pwm.writeMicroseconds(servoPin, servo_pulselength);                   // Writes the mapped value to steer the wheels
  }

  // Checks if the button was pressed recently, if not it will change its output
  // Changes the light output
  if (time3 - previoustime >= 10)
  {
    if (mydata.light == 1)
    {
      switch (light1)
      {
      case 0:
        digitalWrite(lightpin, HIGH);
        light1 = 1;
        previoustime = time3;
        break;
      case 1:
        digitalWrite(lightpin, LOW);
        light1 = 0;
        previoustime = time3;
        break;
      }
    }
  }

  // Changes the mode variable
  if (time2 - previoustime2 >= 10)
  {
    if (mydata.alone == 1)
    {
      switch (mode)
      {
      case 0:
        mode = 1;
        previoustime2 = time2;
        break;
      case 1:
        mode = 0;
        previoustime2 = time2;
        break;
      }
    }
  }

  // Increments the time variables to check in the future if the respective variables can be changed

  time1++;
  time2++;
  time3++;

  // Writes to Serial for debbuging
  Serial.print("\nSteer:  ");
  Serial.print(mydata.steer);
  Serial.print("  Steer pulse: ");
  Serial.print(servo_pulselength);
  Serial.print("  Velocity:  ");
  Serial.print(mydata.velocity);
  Serial.print("  Motor pulse:  ");
  Serial.print(motor_pulselength);
  Serial.print("  Diferença: ");
  Serial.print(time1 - previoustime1);
  Serial.print("  Modo: ");
  Serial.print(mode);
  Serial.print("  Chanell: ");
  Serial.print(radio.getChannel());

  delay(10);
}

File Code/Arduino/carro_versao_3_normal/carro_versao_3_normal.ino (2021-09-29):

//librarias
#include <Servo.h>                                     //Inclui a libraria para o servo  
#include <SPI.h>
#include <nRF24L01.h>                                  //Inclui a libraria para comunicaçao por ondas de radio
#include <RF24.h>                                      //Inclui a libraria para comunicaçao por ondas de radio
#include <TinyGPS++.h>                                 //Inclui a libraria para o GPS
#include <printf.h>


//Define o objeto servo e motor
Servo servo;
Servo motor;

//GPS
static const uint32_t GPSBaud = 9600;                 //Atribui a baudRate para comunicar entre o arduino e o GPS

TinyGPSPlus gps;                                      //Define o objeto gps


//Comunicacao Radio
const byte slaveAddress[6] = "00001";
const byte masterAddress[6] = "00002";

RF24 radio(7, 53); // CE, CSN


//Estrutura com a informacao recebida
struct RECEIVE_DATA_STRUCTURE {
  int velocity;
  int steer;
  int light;
  int freio;
  int alone;
} ;


RECEIVE_DATA_STRUCTURE mydata;                                   //Atribui um nome mais facil de utilizar


//Estrutura com a informacao enviada
struct SEND_DATA_STRUCTURE {
  float longitude0;                                            //4 bytes
  float latitude0;                                             //4 bytes
  int velocity;                                            //4 bytes
  int steer;                                                //4 bytes
} ;


SEND_DATA_STRUCTURE datasend;                                   //Atribui um nome mais facil de utilizar



//Variaveis gerais
#define Baud 115200                                              //Atribui a baudRate para comunicar entre o arduino e o computador
#define steerc 90                                             //Centro das rodas
#define steerd 15                                              //Maximo as rodas podem virar
#define lightpin 46                                              //Define o pino das luzes

//Variaveis
bool rslt;                                                     //Resultado de envio de mensagem
int light1 = 0;                                                //Luzes desligadas
long tempoanterior = 0;                                        //Altura em que foi alterada as luzes
long tempo = 0;                                                //Tempo que nao foi ativado o comando das luzes
long tempoanterior1 = 0;                                       //Tempo da altura em que foi alterada
long tempo1 = 0;
long tempoanterior2 = 0;                                       //Time on the last command
long tempo2 = 0;
int modo = 0;                                                  //Define se está no modo manual ou automatico



void setup() {
  servo.attach(10);                                              //Inicia o Servo
  servo.write(steerc);                                          //Centra as Rodas
  motor.attach(6);                                              //Inicia o motor
  motor.write(90);                                              //Define o ponto morto do motor
  pinMode(lightpin, OUTPUT);                                    //Inicia o pino das luzes
  digitalWrite(lightpin, LOW);                                  //Inicializa as luzes no modo desligado
  Serial.begin(Baud);                                           //Inicializa a comunicaçao Serial com o computador
  printf_begin();

  //Inicia o Radio
  radio.begin();
  radio.openReadingPipe(0, slaveAddress);
 // radio.enableAckPayload();
  radio.startListening();
  //radio.writeAckPayload(0, &datasend, sizeof(datasend)); // pre-load data

  //Inicia a comunicaçao Serial para o GPS
  Serial1.begin(GPSBaud);
}


void loop() {
  //GPS

  while (Serial1.available() > 0) {
    gps.encode(Serial1.read());
    if (gps.location.isUpdated()) {
      datasend.latitude0 = gps.location.lat();
      datasend.longitude0 = gps.location.lng();
    }
  }

  if ((tempo1 - tempoanterior1) >= 20) {
    motor.write(90);
    servo.write(90);
    mydata.steer = 90;
    mydata.velocity = 90;
  }

  else {
    //Nrf24
      if (radio.available())  {            //Looking for the data.
        radio.read(&mydata, sizeof(mydata));    //Reading the data
        tempoanterior1 = tempo1;
    }
  }

  if  (modo == 0) {
    if (mydata.steer < 74 || mydata.steer > 105 || mydata.velocity > 110 || mydata.velocity < 70 ) {
    motor.write(90);
    servo.write(90);
  }
  else {
    //Velocity
    motor.write(mydata.velocity);

    //Steer
    servo.write(mydata.steer);
  }
    datasend.steer = mydata.steer;
    datasend.velocity = mydata.velocity;
  }

  //luzes
  if (tempo - tempoanterior >= 10) {
    if (mydata.light == 1) {
      switch (light1) {
        case 0:
          digitalWrite(lightpin, HIGH);
          light1 = 1;
          tempoanterior = tempo;
          break;
        case 1:
          digitalWrite(lightpin, LOW);
          light1 = 0;
          tempoanterior = tempo;
          break;
      }
    }
  }

  //Envia a informaçao do carro para o comando
  //radio.writeAckPayload(0, &datasend, sizeof(datasend)); // load the payload for the next time

  //Comuta a variavel modo
  if (tempo2 - tempoanterior2 >= 10) {
    if (mydata.alone == 1) {
      switch (modo) {
        case 0:
          modo = 1;
          tempoanterior2 = tempo2;
          break;
        case 1:
          modo = 0;
          tempoanterior2 = tempo2;
          break;
      }
    }
  }


  //Incrementa as variaveis de tempo para futuramente trocar as respetivas variaveis
  tempo++;
  tempo1++;
  tempo2++;


  //Escreve no Serial para debug
  Serial.print("  Velocity:");
  Serial.print(mydata.velocity);
  Serial.print("  Steer:");
  Serial.print(mydata.steer);
  //Serial.print("Light carro: ");
  //Serial.println(light1);
  ///Serial.print("Travao:");
  //Serial.println(mydata.freio);
  Serial.print("  Diferença: ");
  Serial.print(tempo1 - tempoanterior1);
  Serial.print("  Modo:");
  Serial.print(modo);
  Serial.print("  Latitude= ");
  Serial.print(datasend.latitude0, 6);
  Serial.print(" Longitude= ");
  Serial.println(datasend.longitude0, 6);

  delay(20);
}

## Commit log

2021-09-29 First files
    Creation of the repository
    [2 gear.SLDPRT, 8 PIN HEADER, IC, BTS7960 43A HIGH POWER H BRIDGE MODULE.SLDPRT, ALUMINUM ELECTROLYTIC CAPACITOR, 330 uF, BTS7960 43A HIGH POWER H BRIDGE MODULE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]
2021-10-10 Folders renaming
    [2 gear.SLDPRT, 8 PIN HEADER, IC, BTS7960 43A HIGH POWER H BRIDGE MODULE.SLDPRT, ALUMINUM ELECTROLYTIC CAPACITOR, 330 uF, BTS7960 43A HIGH POWER H BRIDGE MODULE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]
2021-10-15 updated assembly
    [ArduinoMega.SLDPRT, BDESC-S10E-RTR brushed motor speed controller ESC.stp.SLDPRT, Blank PCB Project.sldasm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]
2021-10-22 Eletrical Schematic
    [Assem1.SLDASM, Blank PCB Project.sldasm, BoardOutline_Assem1.sldprt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]
2021-11-18 Updates in the assembly
    [Braco inferior-frente.SLDPRT, Braco inferior.SLDPRT, Braco superior frente.SLDPRT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]
2021-11-28 Uploaded 3D parameters images and corrected an hyperlink
    [Controller_Code.ino]
2021-11-29 added 3d printer image
2021-11-29 added schematics image
2022-02-09 Change in the overall of the chassi plus srtarting to use the servo driver to control the esc and servo
    [90headerMale.SLDPRT, Antenna assy.SLDASM, Antenna base.SLDPRT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]
2022-02-09 Working on the adafruit library for servo driver
2022-02-09 Added datasheet for servo and update servo pulse
2022-02-09 motor was able to synchronyze
2022-02-11 changed the pwm signal to microseconds so can input the min and max from the datasheet directly
2022-02-11 Commented the new changes and corrected spelling mistakes
    [Car_Code.ino, Controller_Code.ino]
2022-02-13 Changed the center wheel parameter
2022-02-13 changed steer parameters
2022-02-13 corrected some merging issues
    [Controller_Code.ino]

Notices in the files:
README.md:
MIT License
